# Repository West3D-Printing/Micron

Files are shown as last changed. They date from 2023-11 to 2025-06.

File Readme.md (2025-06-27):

# **Please note this document is a work in progress and will be updated periodically.**
While generally consistent with generic Micron builds the information here is intended specifically for [West3D's Micron+ kit](https://west3d.com/products/micron-plus-180-self-source-configurator-by-west3d-printers-for-ants). If you find errors, omissions, or have suggestions please feel free to open an issue.

# Printed parts, manual, CAD
- Your main source of information is Hartk's GitHub repo: https://github.com/PrintersForAnts/Micron. Please read through this document before you start printing your parts, as there are some modifications we recommend.
- When printing parts be sure to use the 180 files.
- When printing the panel clips you should use the 3mm foam variants.
- We found it useful to have an extra PCB DIN clip to use for securing wires (more on that later).
- These modified Z belt covers work well and give a little more clearance for the A/B motors: https://github.com/PrintersForAnts/Micron/tree/main/Mods/Kayos%20Maker/Flat%20Z%20Belt%20Covers/STLs
- A modified bowden tube entry that adds an ECAS fitting can be found in this repository
- If you plan on moving the printer often this spool holder is convenient: https://www.printables.com/model/542953-voron-v02-foldable-spool-holder
# Toolhead
There are several toolhead choices. The BOM stock toolhead is the Mini Stealthburner.

Our choice is the Dragonburner. The Dragonburner (or Rapidburner) offer better part cooling with two 4010 blowers. You can get the files at https://github.com/chirpy2605/voron/tree/main/V0/Dragon_Burner. You need to use the STL files in the v0.2 directory. There's even a cowl with the Micron logo!

We usually pair the Dragonburner with the Orbiter 2 extruder, but there are many compatible options including G2SA.

A few notes on toolhead boards:
- If you're using the Pancake toolhead board and harness you can get the toolhead board mount at https://github.com/christophmuellerorg/voron_0_pancake_board. This will put the toolhead harness at a 45º angle but works fine.
- If you're using the EBB36 CAN board we recommend the mount by KayosMaker at https://github.com/KayosMaker/CANboard_Mounts/tree/main/STLs/BTT_EBB36_1.0_Mounts

Please note that if you are using the pancake board with 24v fans you will need to cut the trace(s) between pads 1&2 and solder jump pads 2&3:
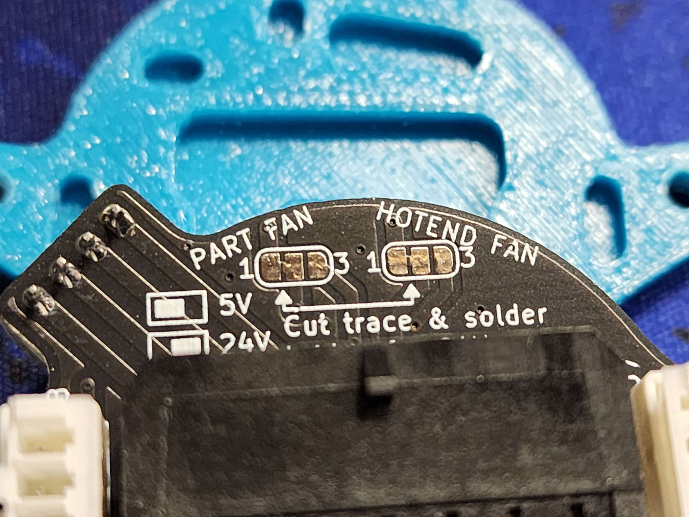
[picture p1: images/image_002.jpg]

Photo courtesy of ZombieHedgehog
# Toolhead mount & probe
- We recommend using Boop as the toolhead mount and Z probe/endstop. You can get the files at https://github.com/PrintersForAnts/Boop/tree/main
- The DragonBurner toolhead requires a modified Boop front: https://github.com/chirpy2605/voron/tree/main/general/Alternative_Voron_Mounts

# Screen
PLEASE NOTE: This pertains to the older revision of the Micron+ and isn't needed for R1

We recommend the BTT TFT43 screen if you're using a Raspberry Pi. If you're using a BTT Pi we recommend you either don't use a screen or source a different option; the BTT TFT35 SPI screen doesn't meet our usability requirements. You will need:
- The mount in the BTT_TFT43 folder in this repository
- The front skirt, accent, and bezel files from https://github.com/PrintersForAnts/Micron/tree/main/Mods/hartk1213/180/Waveshare4.3

# Electronics bay
Our kit uses a slightly different electronics layout for convenience. Looking at the electronics bay (note that your kit may have different motors):
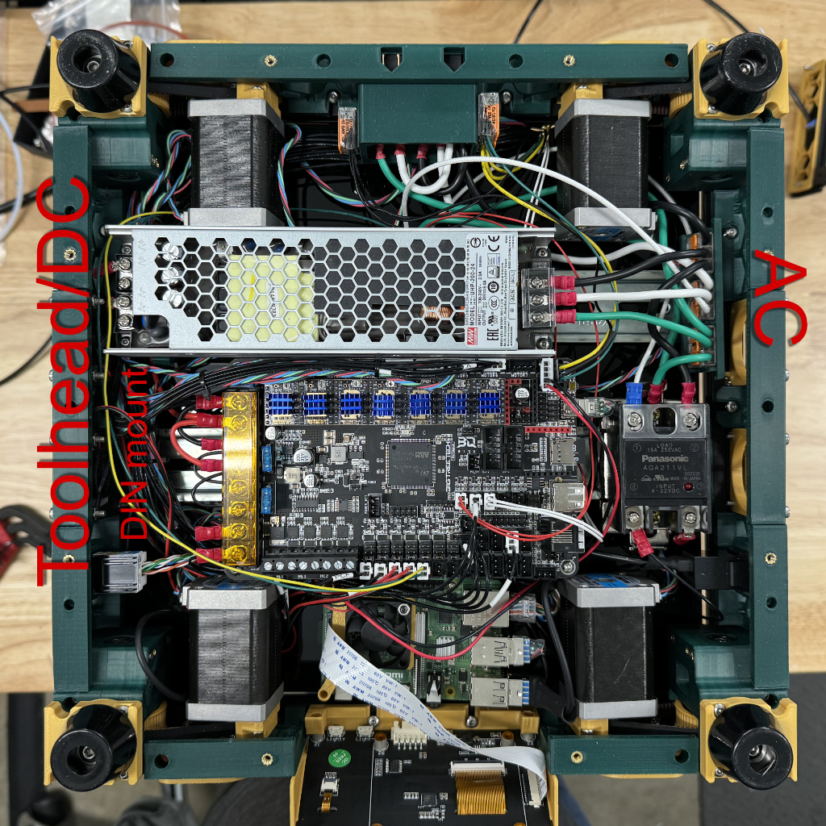
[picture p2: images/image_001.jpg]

- The first DIN rail mounts the PSU and a DIN mount for 3x three port Wagos.
- The second DIN rail mounts the controller board and SSR for the bed.
<br><br>This lets us keep the AC wiring short and contained to the right side (in this view) of the electronics bay. The toolhead wiring and most of the DC wiring is the run on the left side of the bay. We found it helpful to install a DIN rail mount next to the left side of the controller board to tie off wires.

Please note that the spade lugs don't slide into the AC input screw terminals; you need to remove the screw, put the lug in from the top, then replace the screw. The terminal block is designed to capture the lug so it can't slide out if the screw loosens.
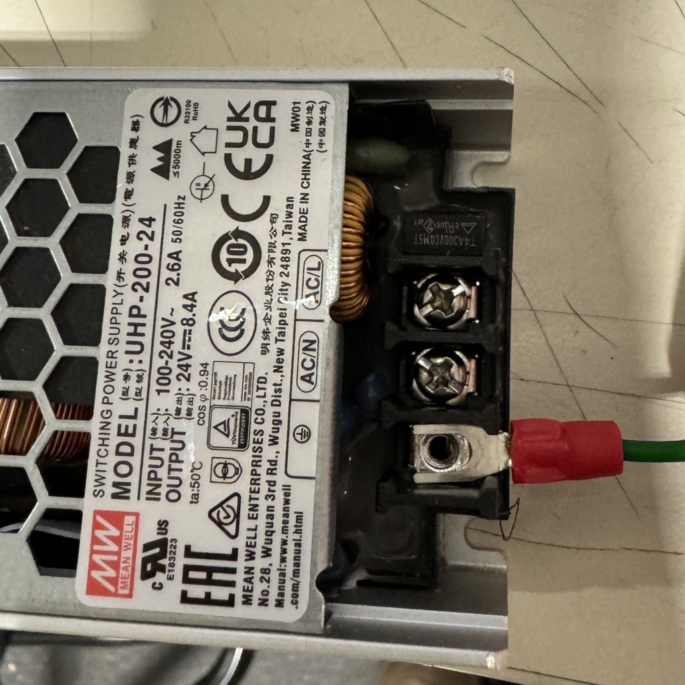
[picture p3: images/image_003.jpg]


# Wiring info
|Use|Wire|Color|Connector 1|Connector 2|Length|Notes|
|---|---|---|---|---|---|---|
|Power inlet to switch Live|18GA|Blue|Quick disconnect - Spade 1/4"|Quick disconnect - Spade 1/4"|70mm||
|Power inlet to switch Neutral|18GA|Brown|Quick disconnect - Spade 1/4"|Quick disconnect - Spade 1/4"|70mm||
||||||||
|Power switch to Wago distribution Live|18GA|Blue|Quick disconnect - Spade 1/4"|Bare - Stripped|190mm||
|Power switch to Wago distribution Neutral|18GA|Brown|Quick disconnect - Spade 1/4"|Bare - Stripped|200mm||
|Power switch to Wago distribution Ground|18GA|Green/Yellow|Quick disconnect - Spade 1/4"|Bare - Stripped|260mm||
||||||||
|Ground Wago to UHP|18GA|Green/Yellow|Bare - Stripped|Spade lug|95mm||
|Ground Wago to SSR lug|18GA|Green/Yellow|Bare - Stripped|Spade lug|65mm||
|SSR lug to bed|18GA|Green/Yellow|Quick disconnect - Spade|bare|300mm||
||||||||
|Live Wago to SSR terminal 2|18GA|Blue|Bare - Stripped|Spade lug|95mm||
||||||||
|Octopus Bed + to SSR|20GA|Red|Spade lug|Spade lug|290mm||
|Octopus Bed - to SSR|20GA|Black|Spade lug|Spade lug|290mm||
||||||||
|UHP to BTT Pi +|20GA|Red|Spade lug|Ferrule|290mm||
|UHP to BTT Pi -|20GA|Black|Spade lug|Ferrule|290mm||
||||||||
|UHP to Octopus power + and motor power +|18GA|Red|Spade lug|Spade lug|170mm|Y cable, 50mm to second spade lug|
|UHP to Octopus power - and motor power -|18GA|Black|Spade lug|Spade lug|170mm|Y cable, 50mm to second spade lug|

# Keystone skirts
There is a modified skirt corner with a connector keystone included in this repository. It can be used to add keystone connectors for USB or Ethernet as shown in the photo above. Credit to Hartk, we took the keystone from his V0.2 mod and mashed it into the Micron.

There are skirts available on Printables with keystones in the back but we preferred not running the data lines to the back. If you'd like the rear facing connectors the mod is available at https://www.printables.com/model/531160-micron-smol-hex-skirts-with-optional-keystone-rear

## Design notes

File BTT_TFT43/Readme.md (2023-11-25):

Modified mount from https://github.com/PrintersForAnts/Micron/tree/main/Mods/hartk1213/180/Waveshare4.3 to fit the BTT TFT43 screen. You will need to download one of the bezels from Hartk's repo.

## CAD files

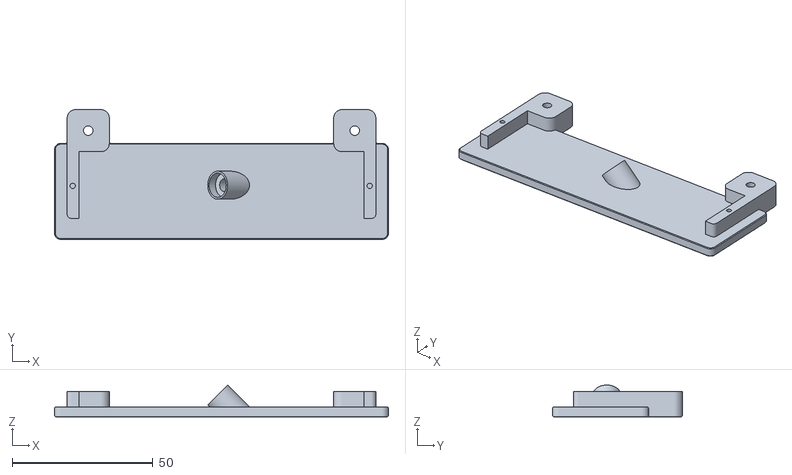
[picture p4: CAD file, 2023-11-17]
Bowden_tube_entry/ECAS_bowden_tube_entry.stl
118.8 x 46.2 x 11.4

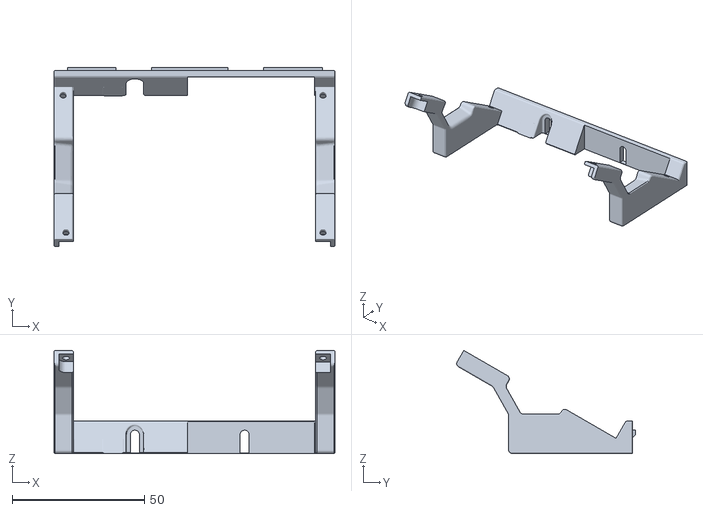
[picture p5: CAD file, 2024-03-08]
BTT_TFT43/STL/Rigid TFT43 mount v5.stl
106.3 x 67.6 x 39.0

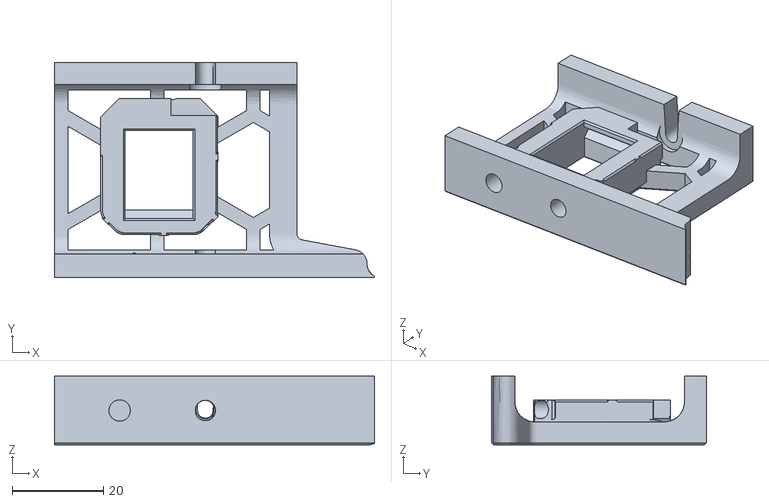
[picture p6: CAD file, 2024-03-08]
Skirt keystone/Micron Skirt keystone.stl
70.0 x 47.0 x 15.0

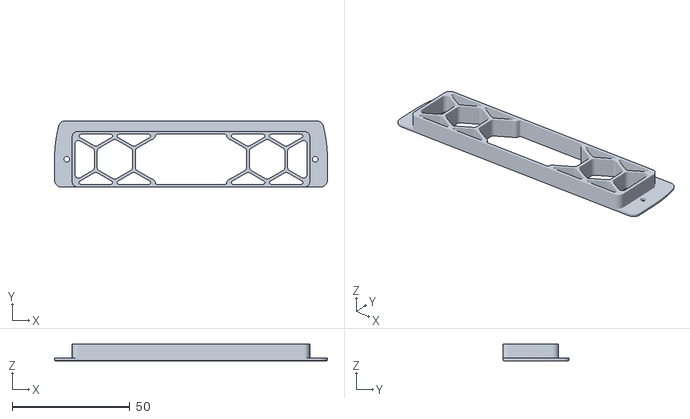
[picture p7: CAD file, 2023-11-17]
Bowden_tube_entry/[a]_ECASbowden_tube_entry_grill.stl
116.1 x 28.2 x 7.20

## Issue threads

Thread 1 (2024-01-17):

Boop Front

Cottean, 2024-01-17:
Invalid link:
The DragonBurner toolhead requires a modified Boop front: https://github.com/chirpy2605/voron/blob/main/general/Experimental/Boop/boop_front.stl

Cottean, 2024-01-17:
Looks like it was moved to https://github.com/chirpy2605/voron/tree/main/general/Alternative_Voron_Mounts

allenrowand, 2024-02-14:
Fixed, thank you

Closed 2024-02-14.

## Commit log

2023-11-16 Upload TFT43 STLs
    [TFT43_bezel.stl, TFT43_mount.stl]
2023-11-17 Update readme, initial upload of bowden tube entry
    [ECAS_bowden_tube_entry.stl, [a]_ECASbowden_tube_entry_grill.stl]
2023-11-17 Updating readme and file names
    [ECAS_bowden_tube_entry.stl, [a]_ECASbowden_tube_entry_grill.stl]
2023-11-17 Edit readme, upload second version of TFT43 mount
    [TFT43_mount_2.stl]
2023-11-18 Update rigid display mount
    [TFT43_mount_2.stl, TFT43_mount_rigid.stl]
2023-11-25 Upload final rigid display mount
    [Rigid TFT43 mount v5.stl, TFT43_bezel.stl, TFT43_mount.stl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]
2023-11-27 Upload skirt keystone STL
    [Micron Skirt keystone.stl]
2023-11-27 Rename skirt mod
    [Micron Skirt keystone.stl]
2023-12-20 Update readme; upload pancake board image
2023-12-22 Update readme; upload screw terminal image
2024-01-03 Begin adding wiring info
2024-03-08 Reorient STLs for printing
    [Micron Skirt keystone.stl, Rigid TFT43 mount v5.stl]
